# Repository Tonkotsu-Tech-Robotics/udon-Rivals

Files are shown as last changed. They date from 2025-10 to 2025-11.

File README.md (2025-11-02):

# UDON V2 | Rivals Robotics Competition
UDON V2 ISO Picture:
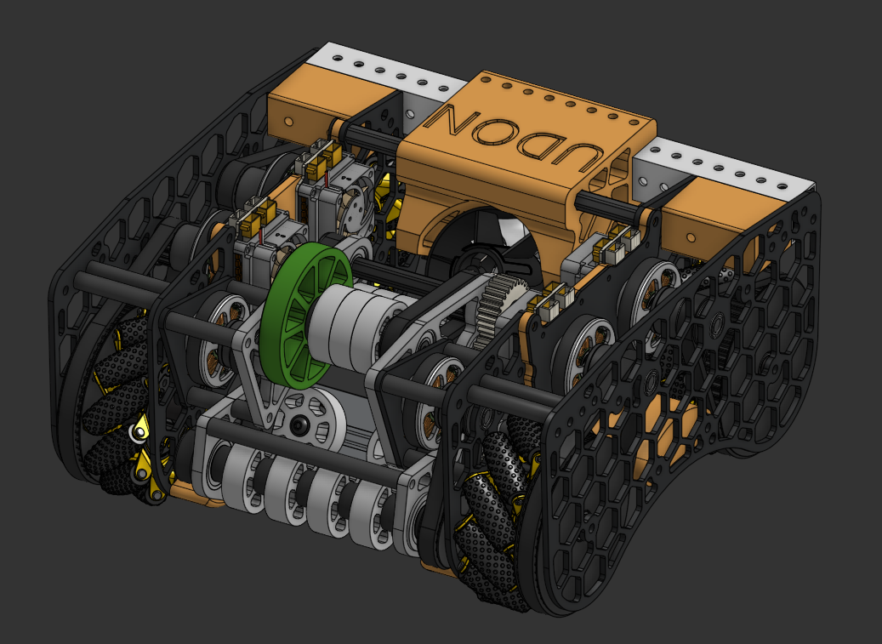
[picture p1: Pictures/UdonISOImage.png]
UDON ISO render


Onshape Link:
https://cad.onshape.com/documents/64d3a7b3a5a997c633685ba5/w/7495e428fcc4a5cb4c65dc9c/e/3e5da57740d178980547a374 

Feel free to make a copy and use it as a base for your robot!

## Rival Robotics
RIVAL Robotics Competition is a robotics competition for all ages targeted at advanced builders. There are multiple events with a different challange each year. For more information, visit https://www.rivalrobotics.co/

## Highlights
- 12x12 Mecanum Drive Base
- Compliant Shuttlecock Intake
- L1, L2 Shooter
- EDF Blower
- Silo Dumper

## Overview
UDON V2 is a shooter robot meant to compete in the Rival Robotics Competition. Its main goal is to shoot missiles (badminton shuttlecock) onto platforms on the goal post.

<table>
  <tr>
    <td valign="top" width="80%">
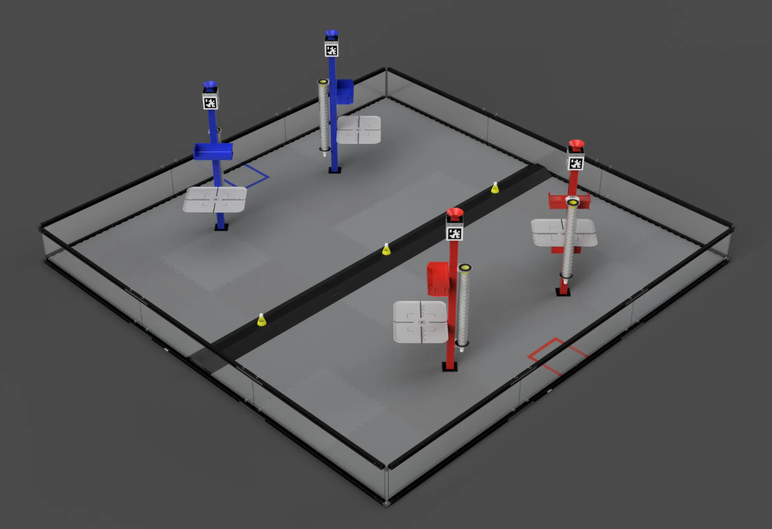
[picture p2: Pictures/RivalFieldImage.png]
Field ISO Render
      
    </td>
    <td valign="top">
        Image of the Rival Robotics "DOOMSDAY" Field
    </td>
  </tr>
</table>

This robot intakes the missiles off the ground to shoot it up into the L2 platforms. It also has the ability to "silo dump" or drop all the missiles out of the tube. The EDF on the back of the robot allows for large area "acquisition" of the missiles and blow it to the other side.

### Why?
UDON V2 was created in order to explore further levels of advanced robotics. Coming from an FRC and Robotics background, UDON acts as a way to build and learn skills as well as grow the RIVAL community. Tonkotsu Tech, the overarching group overseeing UDON, has made contributions to RIVALS and wishes to continue that through UDON.

## Pictures:
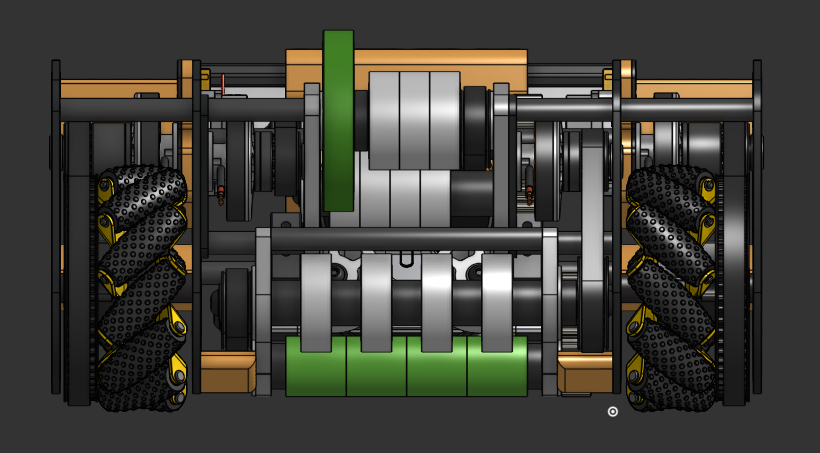
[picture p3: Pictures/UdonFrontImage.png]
UDON Front View

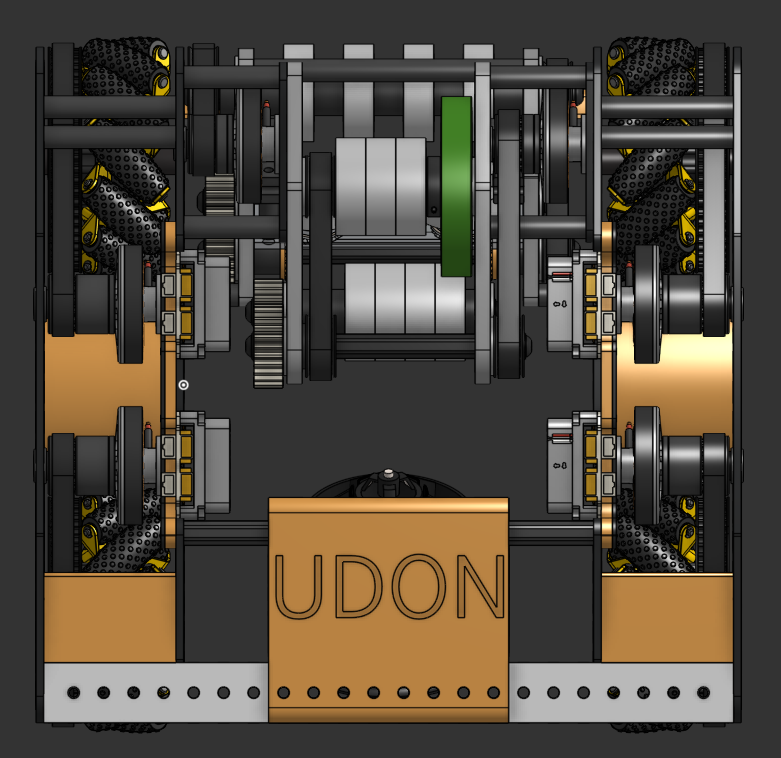
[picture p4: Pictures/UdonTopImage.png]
UDON Top View


## Control System
UDON V2 is based off the moteus control system (https://mjbots.com/) which is a high precision control system with the Raspberry Pi 4 at its core. 

- Raspberry Pi 4
- pi3Hat r4.5
- moteus-r4 Motor Controller
    - Controls 6 5010 Brushles Motors
- mjpower-ss

## Bill of Materials List:

You can download the full CSV here: [bom.csv](bom.csv)
<table>
  <colgroup>
    <col width="8%" />
    <col width="62%" />
    <col width="10%" />
    <col width="8%" />
    <col width="6%" />
    <col width="6%" />
  </colgroup>
  <thead>
    <tr>
      <th align="left">Vendor</th>
      <th align="left">Item</th>
      <th align="right">SKU</th>
      <th align="right">Cost</th>
      <th align="right">Amount</th>
      <th align="right">Total</th>
    </tr>
  </thead>
  <tbody>
    <tr>
      <td>WCP</td>
      <td>1.625" OD x 1/2" Wide Straight Flex Wheel (1/2" Hex Stretch, 30A)</td>
      <td align="right">WCP-1281</td>
      <td align="right">$2.99</td>
      <td align="right">4</td>
      <td align="right">$11.96</td>
    </tr>
    <tr>
      <td>WCP</td>
      <td>1.625" OD x 1/2" Wide Straight Flex Wheel (1/2" Hex Stretch, 45A)</td>
      <td align="right">WCP-1282</td>
      <td align="right">$2.99</td>
      <td align="right">9</td>
      <td align="right">$26.91</td>
    </tr>
    <tr>
      <td>WCP</td>
      <td>.375" OD x .159" ID Rounded Hex Stock (36")</td>
      <td align="right">WCP-0911</td>
      <td align="right">$19.99</td>
      <td align="right">1</td>
      <td align="right">$19.99</td>
    </tr>
    <tr>
      <td>WCP</td>
      <td>43t x 9mm Wide Timing Belt (HTD 5mm)</td>
      <td align="right">WCP-0511</td>
      <td align="right">$3.99</td>
      <td align="right">2</td>
      <td align="right">$7.98</td>
    </tr>
    <tr>
      <td>WCP</td>
      <td>Shipping + Tax</td>
      <td align="right"></td>
      <td align="right">$25.41</td>
      <td align="right">1</td>
      <td align="right">$25.41</td>
    </tr>
    <tr>
      <td>SWYFT</td>
      <td>HTD 5mm Pitch Timing Belts 75T 9mm</td>
      <td align="right"></td>
      <td align="right">$2.74</td>
      <td align="right">4</td>
      <td align="right">$10.96</td>
    </tr>
    <tr>
      <td>SWYFT</td>
      <td>HTD 5mm Pitch Timing Belts 50T 9mm</td>
      <td align="right"></td>
      <td align="right">$2.49</td>
      <td align="right">1</td>
      <td align="right">$2.49</td>
    </tr>
    <tr>
      <td>SWYFT</td>
      <td>HTD 5mm Pitch Timing Belts 45T 9mm</td>
      <td align="right"></td>
      <td align="right">$2.49</td>
      <td align="right">1</td>
      <td align="right">$2.49</td>
    </tr>
    <tr>
      <td>SWYFT</td>
      <td>Shipping Costs</td>
      <td align="right"></td>
      <td align="right">$10.55</td>
      <td align="right">1</td>
      <td align="right">$10.55</td>
    </tr>
    <tr>
      <td>Fabworks</td>
      <td>Mecanum Frame Plates</td>
      <td align="right">25-10-5300</td>
      <td align="right">$142.10</td>
      <td align="right">1</td>
      <td align="right">$142.10</td>
    </tr>
    <tr>
      <td>Amazon</td>
      <td>4010 Fans 12V - 8500RPM</td>
      <td align="right"></td>
      <td align="right">$8.99</td>
      <td align="right">1</td>
      <td align="right">$8.99</td>
    </tr>
    <tr>
      <td>Amazon</td>
      <td>CNHL 2200mAh 4S Lipo Battery 40C</td>
      <td align="right"></td>
      <td align="right">$39.99</td>
      <td align="right">1</td>
      <td align="right">$39.99</td>
    </tr>
    <tr>
      <td>Amazon</td>
      <td>Tax</td>
      <td align="right"></td>
      <td align="right">$3.80</td>
      <td align="right">1</td>
      <td align="right">$3.80</td>
    </tr>
    <tr>
      <td></td>
      <td></td>
      <td></td>
      <td></td>
      <td align="right">28</td>
      <td align="right">$313.62</td>
    </tr>
  </tbody>
</table>
BOM Google Sheet: https://docs.google.com/spreadsheets/d/1sjlqb2LRXWe4DsiQw7wpXGaVzfJAuZjR17yt-ZodIWk/edit?usp=sharing

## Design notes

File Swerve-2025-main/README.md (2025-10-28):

# Swerve-2025

A Python implementation of a swerve drive control system for robotics applications.

## Overview

This project provides a modular swerve drive system that controls four swerve modules, each consisting of a drive motor and a steering motor. The system uses the moteus motor controller library with Pi3Hat for communication.

## Features

- Asynchronous motor control using asyncio
- Modular swerve drive architecture
- Support for moteus motor controllers
- Individual module control with speed and angle settings
- Built-in test functions for system validation

## Requirements

- Python 3.7+
- Hardware: moteus motor controllers with Pi3Hat

## Installation

1. Clone the repository:
```bash
git clone https://github.com/Tonkotsu-Tech-Robotics/Swerve-2025.git
cd Swerve-2025
```

2. Install the required dependencies:
```bash
pip install -r requirements.txt
```

## Usage

### Basic Usage

Run the main program:
```bash
python main.py
```

### Hardware Configuration

The system is configured for the following motor layout:
- Bus 1: Drive motor ID 11, Steer motor ID 12
- Bus 2: Drive motor ID 13, Steer motor ID 14
- Bus 3: Drive motor ID 15, Steer motor ID 16
- Bus 4: Drive motor ID 17, Steer motor ID 18

## Dependencies

- asyncio: Asynchronous programming support
- moteus: Motor controller library
- moteus-pi3hat: Pi3Hat communication interface
- wpilib: WPILib robotics library
- wpimath: WPILib math utilities
- pygame: Game development library (for potential joystick input)

## License

This project is licensed under the terms specified in the LICENSE file.

## Contributing

1. Fork the repository
2. Create a feature branch
3. Make your changes
4. Submit a pull request

## Safety Notes

- Ensure proper hardware connections before running the program
- Use appropriate safety measures when working with motors
- Test in a controlled environment before deployment

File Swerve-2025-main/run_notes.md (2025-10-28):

# Setup Guide

Follow the moteus install docs available at

https://github.com/mjbots/pi3hat/blob/master/docs/reference.md#usage-with-client-side-tools

(I'll put the commands down here to run if you are too lazy like I was)

```
sudo apt install python3-pyside2* python3-serial python3-can python3-matplotlib python3-qtconsole libraspberrypi-dev

python -m venv --system-site-packages moteus-venv

sudo bash

source moteus-venv/bin/activate

pip install asyncqt importlib_metadata pyelftools

pip install moteus moteus_gui moteus-pi3hat
```

In the rasp pi, run these commands to get started with running any of the python files

```
sudo bash # Important since you'll have to run the python files in root
cd Swerve-2025
source moteus-venv/bin/activate # If moteus-venv does not exist, follow moteus guide on creating venv and installing required libraries
```

# Motor setup

You will have to figure out what motors you have first (as well as their ids) before doing any calibration. You can run this command to do that.

```
python3 -m moteus.moteus_tool --info
```

NOTE: If you have more than one motor you want to tune, you will have to adjust their IDs individually.

After figuring out what motors you have, run this command:

```
python3 -m moteus_gui.tview -t [motor id]
```

NOTE: If you want to have multiple motors, it can be dash-separated for a range or comma-separated for individual motors. Examples are given below.

Ex: Comma-separated values for tview in ids 11 and 12
```
python3 -m moteus_gui.tview -t 11,12
```

Ex: Dash-separated for tview in ids 1 through 15
```
python3 -m moteus_gui.tview -t 1-15
```

Dash-separated values can be useful for calibration, motor id lookup and looking at the values for multiple motors.

Comma-separated values can be useful for looking at the stats of a single motor at a time.

You may want to change the IDs so they aren't overriding each other (which can happen if there is improper configuration).

You will want to reopen tview if you have it open already (otherwise open it if you don't), but run this command instead:

```
python3 -m moteus_gui.tview -t [current motor id], [desired motor id]
```

Afterwards, go to the terminal in the bottom of tview and run the following:
```
[current id]>conf set id.id [desired id]
```
Wait for the desired ID to be set and for the terminal to reconfigure some stuff, before running this command:
```
[desired id]>conf write
```
You will know if you did it right if after running `[desired id]>conf write`, you get a console message that says `OK`. 

As an example usage of this, I have a motor on ID 3 and want to change that motor to ID 15. I will need to run the following:
```
python3 -m moteus.tview -t 3,15
```
Wait for motors to get configured up.
```
3>conf set id.id 15
```
Wait for tview to redo some configurations
```
15>conf write
```

Quick rundown of the commands we just ran:

The first command opens up tview for IDs 3 and 15. This is needed since the configuration changes right away and as soon as you change the ID to a new one, the motor will no longer be accessible on the old ID.

The second command simply calls on ID 3 to change its motor ID to 15.

The third command calls on the newly set ID 15 to write its changes so that its persistant.

# Calibration

To properly calibrate motors for code running, run this command in the shell AFTER you have sourced into the virtual environment

IMPORTANT: While calibrating, make sure any motor that is being calibrated can freely spin!

If you want to calibrate multiple motors (on different can busses), [motor id here] should be comma-separated

```
python3 -m moteus.moteus_tool -t [motor id here] --calibrate
```

Ex for 2 motors:
```
python3 -m moteus.moteus_tool -t 1,2 --calibrate
```

# Starting the motors

There are several example files that should work fine after calibration, the one that should be used is wait_complete.py.

https://github.com/mjbots/moteus/blob/main/lib/python/examples/wait_complete.py

Before starting motors, make sure to disable servopos position min/max (You only have to do this the first time setting up from the Raspberry Pi). You can do this by first going into tview

```
python3 -m moteus_gui.tview -t [all your motor ids, comma separated]
```

Then, in the command bar at the bottom of the GUI, running

```
[motor id]>conf set servopos.position_min nan
```
```
[motor id]>conf set servopos.position_max nan
```

then running this command to save the configurations

```
[motor id]>conf write
```

IMPORTANT: If you have multiple motors, you will have to run this command for each individual motor in order to prevent issues. If you did it incorrectly, running any code should show error 39 in the fault section of servo_stats in tview. You can check if you did it correctly in tview by running this command in the bottom terminal of tview:

```
[motor id to check]>d stop
[motor id to check]>d pos 20 0 0.5 a5 v5
[motor id to check]>d stop
```

Example usage:
```
12>d stop
12>d pos 20 0 0.5 a5 v5
12>d stop
```

(This will set the position to 20 with an ending velocity of 0, torque of 0.5, and max accel of 5 rev/s^2 and max velocity of 5 rev/s, then stop the motor).

NOTE: In order to completely check for faults, you may want to run that more than once (2 times should be fine).

Setting servo pos max/min to NaN will disable the check that requires the motor position to start within a specific range (from -1 to 1), and this can screw up the motors if you don't have a command that moves the motors into their original starting position.

# Additional Notes

Running the tview GUI will also allow you to graph and track motor telemetry data such as current position, velocity, among other points, making it easier to debug

Viewing errors or faults can be done by going into tview, then servo_stats, and then fault.

SUPER IMPORTANT!!!!!! In any motor.set_position() or motor.set_position_wait_command() function, ALWAYS have a velocity_limit and accel_limit parameter or else ur motor go bye bye :D An example of such is provided down below.

```
await controller.set_position( # Same thing with controller.set_position_wait_complete()
    position=1.0,
    velocity=2.0,
    velocity_limit=5.0,
    accel_limit=4.0
)
```

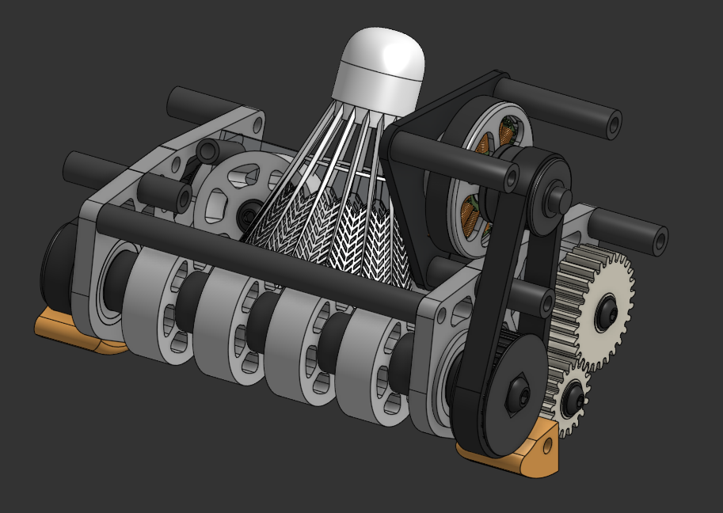
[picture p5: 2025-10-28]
Pictures/IntakeOnlyImage.png

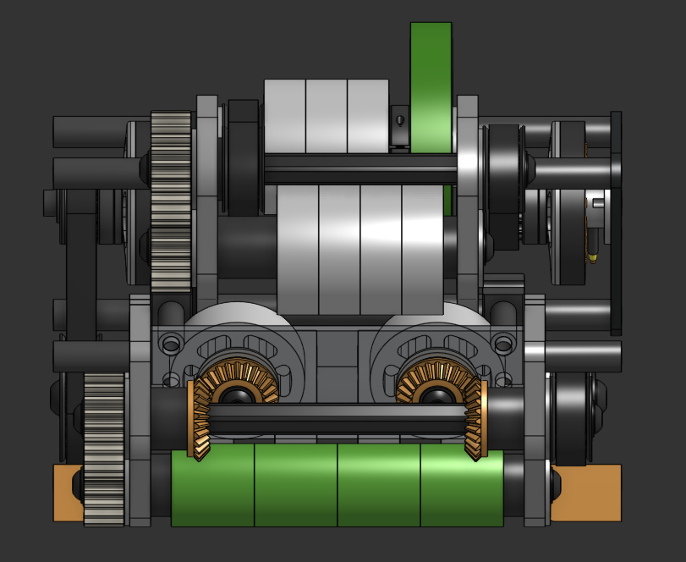
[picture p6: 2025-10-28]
Pictures/IntakeBackImage.png

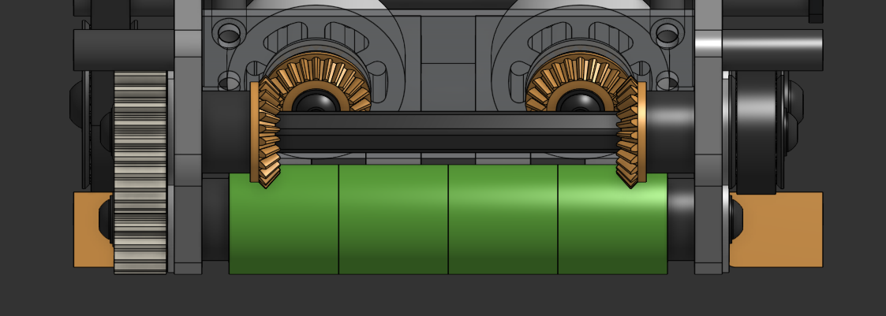
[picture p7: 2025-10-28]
Pictures/BevelGearShowing.png

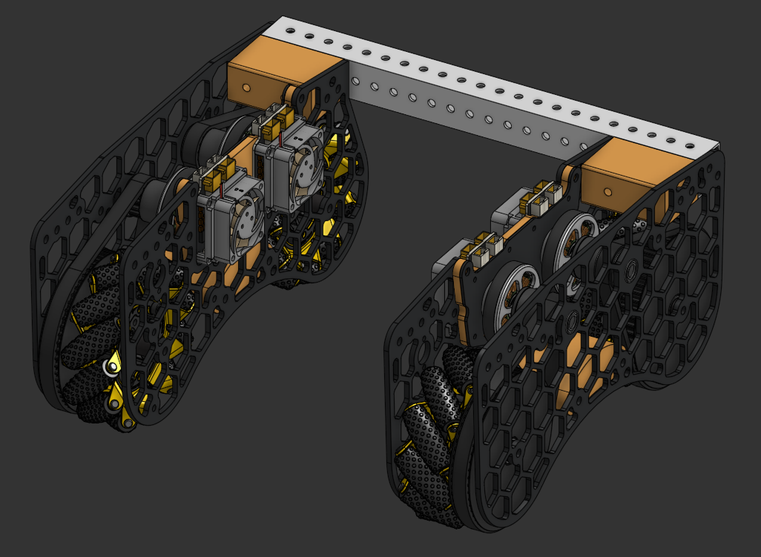
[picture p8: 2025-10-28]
Pictures/BareMecanumDrive.png

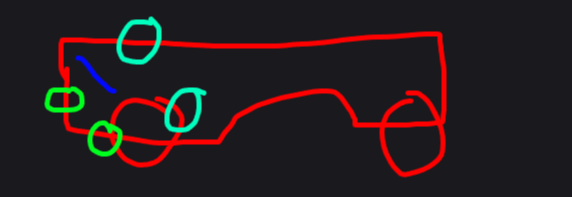
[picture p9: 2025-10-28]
Pictures/UDONSketch.png

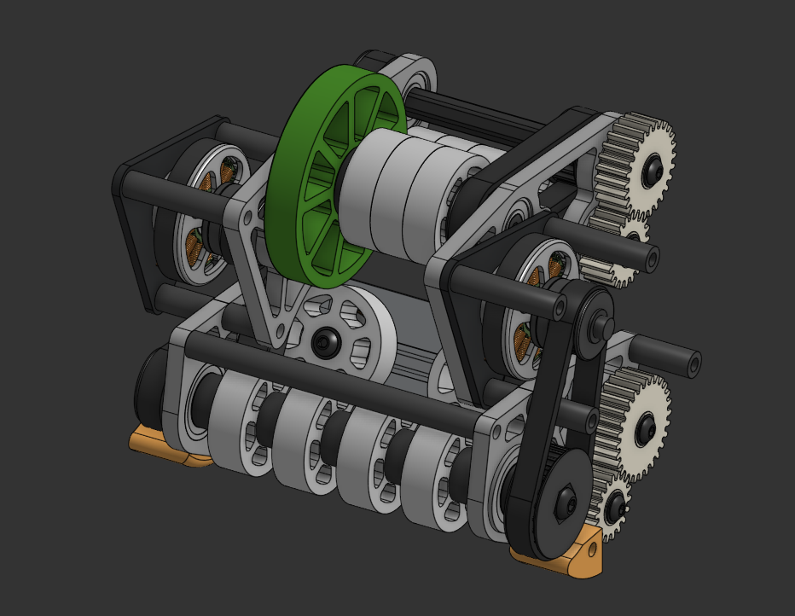
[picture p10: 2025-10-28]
Pictures/IntakeISOImage.png

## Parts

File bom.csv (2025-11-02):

Vendor | Item | SKU | Cost | Amount | Total
WCP | 1.625" OD x 1/2" Wide Straight Flex Wheel (1/2" Hex Stretch, 30A) | WCP-1281 | $2.99 | 4 | $11.96
WCP | 1.625" OD x 1/2" Wide Straight Flex Wheel (1/2" Hex Stretch, 45A) | WCP-1282 | $2.99 | 9 | $26.91
WCP | .375" OD x .159" ID Rounded Hex Stock (36") | WCP-0911 | $19.99 | 1 | $19.99
WCP | 43t x 9mm Wide Timing Belt (HTD 5mm) | WCP-0511 | $3.99 | 2 | $7.98
WCP | Shipping + Tax |  | $25.41 | 1 | $25.41
SWYFT | HTD 5mm Pitch Timing Belts 75T 9mm |  | $2.74 | 4 | $10.96
SWYFT | HTD 5mm Pitch Timing Belts 50T 9mm |  | $2.49 | 1 | $2.49
SWYFT | HTD 5mm Pitch Timing Belts 45T 9mm |  | $2.49 | 1 | $2.49
SWYFT | Shipping Costs |  | $10.55 | 1 | $10.55
Fabworks | Mecanum Frame Plates | 25-10-5300 | $142.10 | 1 | $142.10
Amazon | 4010 Fans 12V - 8500RPM |  | $8.99 | 1 | $8.99
Amazon | CNHL 2200mAh 4S Lipo Battery 40C |  | $39.99 | 1 | $39.99
Amazon | Tax |  | $3.80 | 1 | $3.80
 |  |  |  | 28 | $313.62

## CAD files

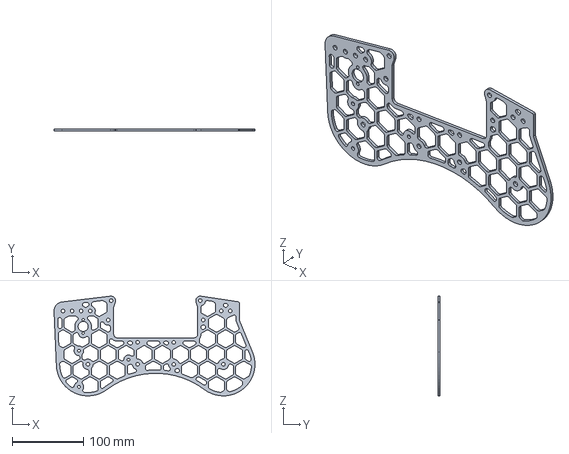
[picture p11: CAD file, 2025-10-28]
CAD/6061 Plates/Inside Plate.step
282.7 x 3.17 x 140.4 mm

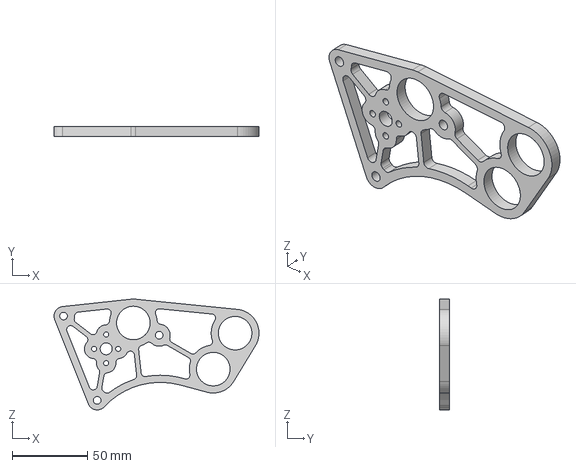
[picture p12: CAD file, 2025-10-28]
CAD/6061 Plates/Shooter Plate Right.step
136.1 x 6.35 x 73.6 mm

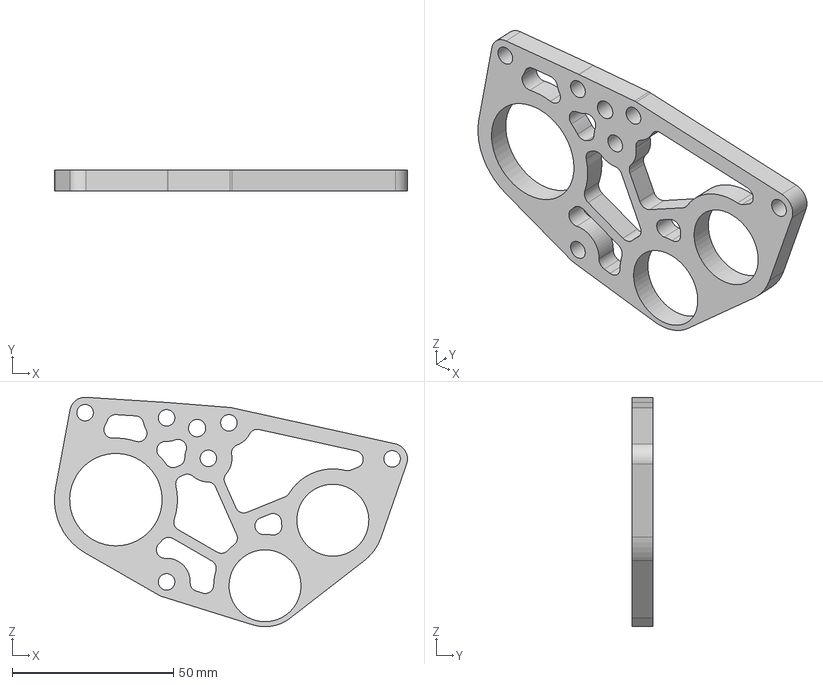
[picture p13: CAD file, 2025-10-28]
CAD/6061 Plates/Intake Plate.step
109.3 x 6.35 x 71.0 mm

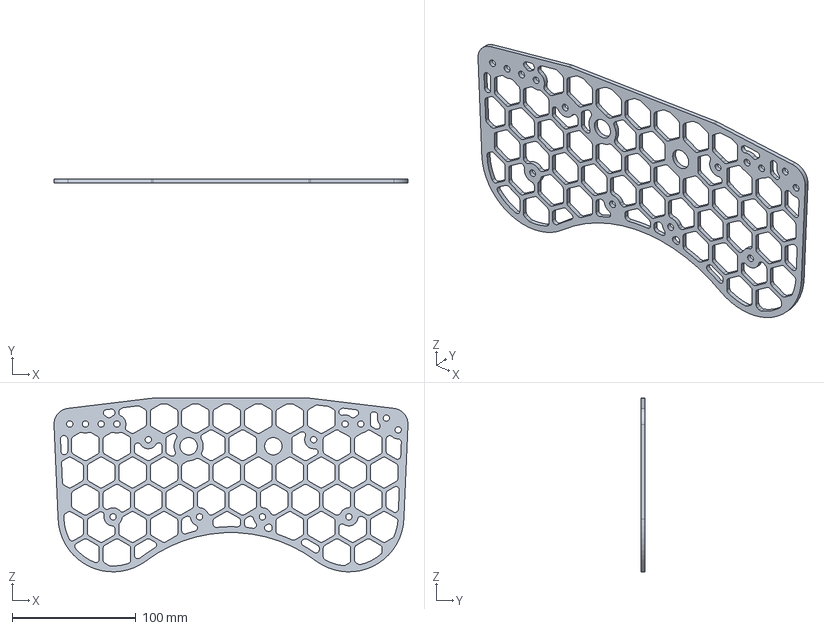
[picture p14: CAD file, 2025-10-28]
CAD/6061 Plates/Outside Plate.step
286.0 x 3.17 x 140.3 mm

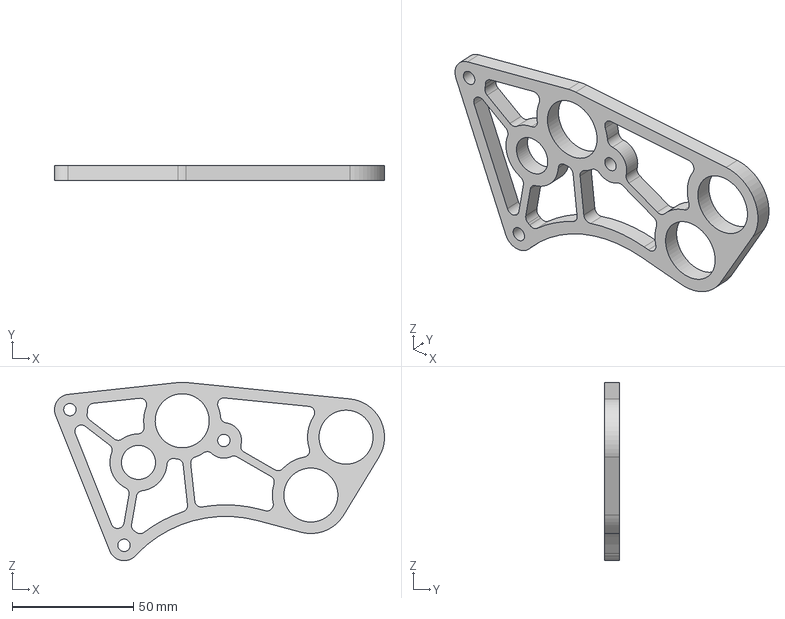
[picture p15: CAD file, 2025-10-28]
CAD/6061 Plates/Motor Plate Left.step
136.1 x 6.35 x 73.6 mm

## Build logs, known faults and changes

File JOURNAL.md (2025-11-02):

<!--
  ===================    !!READ THIS NOTICE!!   ====================
  DO NOT edit this file manually. Your changes WILL BE OVERWRITTEN!
  This journal is auto generated and updated by Hack Club Blueprint.
  To edit this file, please edit your journal entries on Blueprint.
  ==================================================================
-->

## 10/27/2025 7:42 PM - Restarting an Old project  

I've had multiple attempts at building a rival robot, many of which came into fruition but never had enough time to be tuned and refined. This includes Tonkotsu V1 and Tonkotsu V2 which had all the CAD and actual physical build but the swerve drive made it difficult to run well. With UDON, I plan to take a step back and build an easier mecanum drive. Here's what I'm thinking: 


Not great, I know but the mechanism can be changed. The red is the mecanum drive base, green is the intaking wheels, dark blue is the centering wheels, and teal is the shooter. I wanted to base this off NCR rivals bot but as a shooter design instead of an arm that they had. One of the biggest issues here is just how consistent it can be. With the swerve drive I already have, the moteus controllers have very good rpm control but I'm not really sure how well the shooter could consistently hit that same spot. 

Beginning to work on the mecanum drive here: 


Big decision I had to make was what the cool the moteus controllers with. The controllers in the CAD use fans because official heatsinks are ABSURDLY expensive, around 30 dollars each. I've had some controllers burn up in the past and don't wish for that to happen again. Another thing is for some reason, Onshape mirroring causes really bad lag... not really a design problem but something that is really annoying. Reusing what I had, I used the 5010 motor from the swerve but went with a different pinion mounting this time. Last time on the swerve, I bolted in a metal custom cut gear onto the motor directly and it caused a lot of friction between the gears so this time I'm belting it and also having a 3D print and connection to a pinion on top and then holding the other side with a bearing. I think this will help a lot with making the motor movement better (I think that friction caused the burn out of the moteus controller in the swerve).

I think this is a great start, I'm banking on the fact that I can also borrow the GoBilda mecanum wheels from my local FTC team :D  

## 10/27/2025 7:43 PM - CAD Intake  

I've thought about many ways to do the intake, with a shuttlecock being such an oriented-based game piece, the head has to go forward at all times for this to work. I tried to figure out a passive way of intaking but none seems as reliable as having 2 centering wheels.


I'm quite proud of the centering wheels using bevel gear tech, it just looks so good. One of the biggest issues here was trying to figure out how to power the centering wheels. I should have taken a photo of the interferences I was having before but at the time, I didn't plan on powering it using the same motor, I was thinking of just having a separate motor. However, the tight packaging between the mecanum drives didn't allow for another motor, especially because it was horizontal. There were many adjustments I had to make to the positioning of the shaft that holds the bevel gear.


Right now, I'm not exactly sure how I plan to stop the shuttlecock from going all the way through. I didn't find a good way to package and might be leaning towards a usb sensor that connects to the Raspberry Pi because all of the pins are covered by the moteus pi3hat. However, I want to first prototype whether I can get away without that and just not spin the shooter motors and back the shuttcock into place for shooting :)  

## 10/27/2025 7:44 PM - Finished Shooter CAD  

Finally, I found a way to fit in this shooter. The packaging is quite tough and I am slightly worried over the flywheels expanding when it is shooting. I think this is good enough. One other thing is that the green wheel is used for silo dumping but it might get in the way of the shuttlecock, I have to prototype to find out.



I had to commit to the angle as I wasn't going to go back on it. Looking at the arc, it looks okay for shooting but what isn't prototyped yet is the compression. I estimated a 5mm compression out of a 25mm shuttlecock head would be decent but I will never know without trying it. For future journals, I need to start taking more pictures when things go wrong. As said before, packaging was a huge issue, I couldn't figure out how to make the shafts and pullies not touch the side plates. I ended up opting just to have another shaft that goes across so I can split each side evenly with the gears and pullies. 



But now I'm looking back on it, this packaging also means repairability is kind of on the iffy side. Getting to a bolt in this intake is a little bit sus... looking to fix that.  

## 10/27/2025 7:45 PM - EDF Blower Add-on  

Watching back some of the old games from Orange County Maker Fair and Tidal Tumble, EDF seems like the way to go. The EDF blows the shuttlecocks to the other side and since the floor is a point, that is a LOT of points that can be gained that way. I added one to the robot too but I think it needs a cover because in one of the matches, I saw a shuttlecock go into it and it just exploded.



It looks really good but now I have to go back and redesign where I am going to put my electronics. I planned to put it where the EDF is (in the back of the robot) but with that space gone, I might have to add a plate so that I can just put the electronics on the top of the bot. This isn't really ideal because I liked the idea of a flat tanky robot but oh wells.


Credits: NCR 

This is one of the things I need to do in the future. I loved how they packaged their raspberry pi and moteus pi3hat but I'm not sure if I want to do the way they did. On my Raspberry pi stack right now, I have a fan in between to cool the pi but that also means it will be a lot taller. Considering whether I should follow NCR or not...  

## 10/28/2025 - Blueprint!  

Hey everyone! 

I didn't do much today besides just figuring out this blueprint stuff. I got the BOM stuff done and now the project is shipped off! 


Thanks so much for the follows and the views, I hope to be able to show you my progress soon. I'm starting prototyping with 3D prints, especially the intake. One issue I might be seeing is just manufacturing fast enough. Rivals competition is on November 22 so time is of the essence. Thanks for checking this out!

## 10/30/2025 - Fixed My Journals  

Hey everyone!

Update: After shipping the project, I got feedback that I need to fix my journals and make them more in depth with my struggles and my successes. I went back and added a lot of the key parts that I remember. Sorry if I couldn't have much images of all the troubles I had (so many interferences in Onshape because packaging was really tight) but I hope my words are good enough for now. 100% for the future, I will document more and not just take pictures when the final product is done. 


I went ahead and printed some of parts in the intake and shooter. I know it says in the github to cut this out of 6061 aluminum but actually, I found that 3D printing should be strong enough for prototyping. There is some bends so I will go back and print this with no pocketing. Right now, its at an absurd 8 walls and 35% infill and seems to be holding up good!

I hope you all enjoy! See you in the next journal :D

P.S. Got an update from my very first journal, my FTC team was willing to lend me their mecanum wheels! That saves me over 180 dollars :) One bad thing though, went to my FRC team to see if I could use the CNC router to cut the aluminum and it seems like the router isn't working right now... hoping to see if I can help fix it for them and save some more money.  

## 11/2/2025 - Getting This Approved  

Hey everyone!

Sorry for the lack of posts in recent days, I've been talking and working with some Hack Club/Blueprint people that helped me get this approved/into what they want from the project. I truly appreciate all the help from Hack Club members, they are amazing. One of the biggest things that I need to change is just making my BOM cheaper. The way I did this was removing the EDF as it was the one thing in the project that wasn't a stepping stone to build the rest. This was quite sad as I really liked the EDF but unlike the mecanum plates, I need those plates to build the rest of the robot. The EDF can always be added on at the end. 


Here's what it'll look like without the EDF. This was a hard decision but I had to do something to drop the price and be reasonable. I am now down around 80 dollar from the original sitting around $313 instead of $397. I'm not sure whether or not these changes count for hours yet so I will be in contact with Hack Club, for now, I'll just put 0.1 hours.

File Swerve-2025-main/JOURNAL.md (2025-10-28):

<!--
  ===================    !!READ THIS NOTICE!!   ====================
  DO NOT edit this file manually. Your changes WILL BE OVERWRITTEN!
  This journal is auto generated and updated by Hack Club Blueprint.
  To edit this file, please edit your journal entries on Blueprint.
  ==================================================================
-->

## 10/27/2025 - Test  

I'm trying to test whether i need to make a journal in here or the journal in github because the one In github, apparently the hours don't transfer onto the actualhours on the website

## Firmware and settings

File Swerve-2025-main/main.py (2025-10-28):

import asyncio
from Swerve.SwerveDrive import SwerveDrive

async def main(swerve_drive: SwerveDrive = None):
    await swerve_drive.initialize_modules()
    speeds = [0.0, 0.0, 0.0]
    while True:
        speeds = await swerve_drive.getControllerSpeeds()
        await swerve_drive.set_drive_speeds(speeds[0], speeds[1], speeds[2], False)

        
    
if __name__ == '__main__':
    # Initialize SwerveDrive instance
    swerve_drive = SwerveDrive()
    try:
        asyncio.run(main(swerve_drive))
    except KeyboardInterrupt:
        print("Program interrupted by user. Stopping all modules.")
        asyncio.run(swerve_drive.stop())
        exit(0)
    except Exception as e:
        print(f"An unexpected error occurred: {e}")
        asyncio.run(swerve_drive.stop()) 

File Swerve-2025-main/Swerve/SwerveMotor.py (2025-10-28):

import moteus
import moteus_pi3hat
import asyncio
import math

"""
A swerve motor class

Defines all the functions required for motor movement using the moteus library.
"""
class SwerveMotor:
    def __init__(self,
                 motorID: int,
                 transport: moteus_pi3hat.Pi3HatRouter,
                 accel_limit: float=20.0,
                 velocity_limit: float=20.0,
                 watchdog_timeout: float=0.5):
        """
        Constructs a swerve motor instance.

        :param motorID (int): Moteus controller ID.
        :param transport (Pi3HatRouter): Transport object.
        :param accel_limit (float): Acceleration limit in rev/s².
        :param velocity_limit (float): Velocity limit in rev/s.
        :param watchdog_timeout (float): Timeout before function stops running (if you don't know how this param works, better not touch it).
        """

        # Set the local properties to be accessible from within the class.
        self.accel_limit = accel_limit
        self.velocity_limit = velocity_limit
        self.watchdog_timeout = watchdog_timeout
        self.motor = moteus.Controller(id=motorID, transport=transport)

    @property
    async def position(self):
        """
        Gives the current absolute motor position (relative to position 0).

        :return float: The current absolute motor position in revolutions.
        """

        # Query the motor for its current state
        result = await self.motor.set_position(position=math.nan, query=True)

        print(f"Motor {self.motor.id} position register is of type {type(result.values[moteus.Register.POSITION])}")

        # Extract the position from the result
        return result.values[moteus.Register.POSITION]

    @property
    async def velocity(self) -> float:
        """
        Gives the current velocity

        :return float: The current velocity of the motor in rev/s.
        """

        # Query the motor for its current state
        result = await self.motor.set_position(position=math.nan, query=True)

        # Extract the position from the result
        return result.values[moteus.Register.VELOCITY]
    
    @property
    async def values(self) -> list:
        """
        Gives a list of properties exposed by the moteus library for reading or writing.
        The full list can be found here:
        https://github.com/mjbots/moteus/blob/main/lib/python/moteus/moteus.py#L149 (class code)
        https://github.com/mjbots/moteus/blob/main/docs/reference.md#a2b-registers (descriptors)
        
        :returns [any]: A list of Register object properties
        """
        result = await self.motor.set_position(query=True)

        return result.values

    async def setAngle(self, angle_deg: float, transport: moteus.Transport) -> bool:
        """
        A position mode function.
        
        Move to a target angle in degrees.
        Returns boolean and retrived position after rotation

        NOTE: If the wait_time parameter is not set, set_position will not fully run unless you manually implement asyncio.sleep().
        It is better if you implement this yourself IF you have more than 1 motor.

        :param angle_deg (float): An angle in degrees to move to. Will be converted to revolutions. Motor will move  to this angle relative to its current position, and with a max speed of what is set in self.velocity_limit in rev/s. It will reach this max speed in self.accel_limit in rev/s².
        :param transport (moteus.Transport): The transport object to use for communication. Should be the same transport used in every motor.

        :return bool: True if the angle was set successfully, False otherwise.
        """

        try:
            angle_rev = angle_deg / 360.0

            # degAngle = await self.position * 360

            # if degAngle == None:
            #     raise TypeError(
            #         "Degree angle in setAngle function returned as type None")

            # adjustedAngle = angle_rev  # temp angle for now, add calculations in later

            await transport.cycle([self.motor.make_position(
                position=angle_rev,
                accel_limit=self.accel_limit,
                velocity_limit=self.velocity_limit,
                watchdog_timeout=self.watchdog_timeout
            )])

            return True
        except Exception as e:
            print(f"Error caught in setAngle function: {e}")
            await self.emergency_stop(f"Error caught in setAngle function: {e}")
            return False

    async def addToCurrentPos(self, position_val: float, transport: moteus.Transport) -> bool:
        """
        Move to a position in revolutions relative to current position.

        NOTE: If the wait_time parameter is not set, set_position will not fully run unless you manually implement asyncio.sleep().
        It is better if you implement this yourself IF you have more than 1 motor.

        :param position_val (float): The position target to move to in revolutions. This will be added to the current position of the motor, not set as an absolute position.
        :param transport (moteus.Transport): The transport object to use for communication. Should be the same transport used in every motor.

        :return bool: True if the position was set successfully, False otherwise.
        """
        try:
            await transport.cycle([self.motor.make_position(
                position=(position_val + self.position),
                accel_limit=self.accel_limit,
                velocity_limit=self.velocity_limit,
                watchdog_timeout=self.watchdog_timeout)
            ])

            return True
        except Exception as e:
            print(f"Error caught in addToCurrentPosition function: {e}")
            await self.emergency_stop(f"Error caught in addToCurrentPosition function: {e}")
            return False

    async def setPosition(self, position_val: float, transport: moteus.Transport ) -> bool:
        """
        A position mode function.

        Move to an absolute position in revolutions.

        NOTE: If the wait_time parameter is not set, set_position will not fully run unless you manually implement asyncio.sleep().
        It is better if you implement this yourself IF you have more than 1 motor that you want to run.

        :param position_val (float): The position target to move to in revolutions.
        :param transport (moteus.Transport): The transport object to use for communication.

        :return bool: True if the position was set successfully, False otherwise.
        """
        try:
            await transport.cycle([self.motor.make_position(
                position=position_val,
                accel_limit=self.accel_limit,
                velocity_limit=self.velocity_limit,
                watchdog_timeout=self.watchdog_timeout)
            ])
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

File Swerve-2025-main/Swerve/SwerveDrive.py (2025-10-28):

import moteus
import moteus_pi3hat
import asyncio
from Swerve.SwerveModule import SwerveModule
import Utils.Constants as Constants
import wpimath.estimator as estimator
from wpimath.geometry import Pose2d, Rotation2d
import wpimath.kinematics 
from wpimath.geometry import Pose3d, Rotation3d
import math
import wpilib
import numpy as np


from Utils.Controller import Controller

class SwerveDrive:
    def __init__(self):
        self.transport: moteus.Transport = moteus_pi3hat.Pi3HatRouter(
            servo_bus_map={
                1: [11, 12], # Bus 1, Motor ids 11 and 12
                2: [13, 14], # Bus 2, Motor ids 13 and 14
                3: [15, 16], # Bus 3, Motor ids 15 and 16
                4: [17, 18],  # Bus 4, Motor ids 17 and 18
            }
        )

        #need to add controller
        self.controller = Controller()
        self.modules = []
        # pose_estimator: estimator.SwerveDrive4PoseEstimatorBase | None = None
        # pose_estimator_3d: estimator.SwerveDrive4PoseEstimator3dBase | None = None

        # states = [wpimath.kinematics.SwerveModuleState() for _ in range(4)]
        # set_states = [wpimath.kinematics.SwerveModuleState() for _ in range(4)]

        # self.pose_estimator = self.initialize_pose_estimator()
        # self.pose_estimator_3d = self.initialize_pose_estimator_3d()
        # self.field = wpilib.Field2d()

        # self.robot_pos = Pose2d(0.0, 0.0, Rotation2d.fromDegrees(0.0))
        # self.robot_pos_3d = Pose3d(0.0, 0.0, 0.0, Rotation3d(0.0, 0.0, 0.0))

    # this is not my code maybe delete later
    async def stop(self):
        """
        Stops all swerve modules.
        """
        [
            await module.stop() for module in self.modules
        ]

    async def setAll(self, speeds, angles):
        """
        Sets the speed and angle of each swerve module.
        """
        [
            await module.set(speed, angle, self.transport)
            for module, speed, angle in zip(self.modules, speeds, angles)
        ]

    async def setModule(self, index, speed, angle):
        """
        Sets the speed and angle of a specific swerve module.
        """
        await self.modules[index].set(speed, angle, self.transport)

    async def getModulePosition(self, index):
        """
        Gets the position of a specific swerve module.
        """
        return await self.modules[index].getPosition()
    
    async def getControllerSpeeds(self):
        """
        Uses the controller to set the speeds of the swerve modules based on joystick input.
        """
        forward_speed = self.controller.get_axis(Controller.LEFT_X)
        left_speed = self.controller.get_axis(Controller.LEFT_Y)
        turn_speed = self.controller.get_axis(Controller.RIGHT_X)

        return [forward_speed, left_speed, turn_speed]


    # NEW CODE

    async def initialize_modules(self):
        return [
            SwerveModule(
               drive_id=11, steer_id=12, transport=self.transport
            ),
            SwerveModule(
                drive_id=13, steer_id=14, transport=self.transport
            ),
            SwerveModule(
                drive_id=15, steer_id=16, transport=self.transport
            ),
            SwerveModule(
                drive_id=17, steer_id=18, transport=self.transport
            )
        ]
    
    # async def initialize_pose_estimator(self):
    #     return estimator.SwerveDrive4PoseEstimator(
    #         Constants.kinematics,
    #         Rotation2d.fromDegrees(self.get_heading()), #<- needs to be updated
    #         self.get_module_positions(), #<- allso wrong change later
    #         Pose2d(0.0, 0.0, Rotation2d.fromDegrees(0.0)),
    #         np.array([[0.02], [0.02], [math.radians(5)]]),
    #         np.array([[0.3], [0.3], [math.radians(10)]])
    #     )
    
    # async def initialize_pose_estimator_3d(self):
    #     return estimator.SwerveDrive4PoseEstimator3d(
    #         Constants.kinematics,
    #         self.get_rotation_3d_function, #<- needs to be updated
    #         self.get_module_positions(), #<- wrong change later
    #         Pose3d(0.0, 0.0, 0.0, Rotation3d(0.0, 0.0, 0.0))
    # )

    async def swerve_drive_periodic(self):
        # await self.update_pos() 
        return

        #idk why its white 
        # self.pose_estimator.update(self.get_pidgey_rotation(), self.get_module_positions()) #fix more stuff dummy
        # self.pose_estimator_3d.update(self.pidgey.getRotation3d(), self.get_module_positions()) # needs to change the rotation functions here

        # self.robot_pos = self.pose_estimator.getEstimatedPosition()
        # self.robot_pos_3d = self.pose_estimator_3d.getEstimatedPosition()

    # async def update_pos(self):
        # return #no idea how to do this shit rn
    
    async def set_drive_speeds(self, forward_speed, left_speed, turn_speed, is_field_oriented = False):
        # Convert to chassis speeds the robot understand?s
        speeds = None
        if is_field_oriented:
            speeds = wpimath.kinematics.ChassisSpeeds.fromFieldRelativeSpeeds
            (forward_speed, left_speed, turn_speed, self.get_heading_rotation2d())
            #fix get heading

        else: 
            speeds = wpimath.kinematics.ChassisSpeeds(forward_speed, left_speed, turn_speed)

        speeds = wpimath.kinematics.ChassisSpeeds.discretize(speeds, 0.02)

        new_states = Constants.kinematics.toSwerveModuleStates(speeds)

        new_states = wpimath.kinematics.SwerveDrive4Kinematics.desaturateWheelSpeeds(new_states, Constants.MAX_SPEED)
        await self.set_swerve_module_states(new_states)

    async def reset_heading(self):
        #reset the heading
        return

    async def get_swerve_module_states(self) -> wpimath.kinematics.SwerveModuleState:
        current_module_state = wpimath.kinematics.SwerveModuleState()
        for i in range(4):
            current_module_state[i] = self.states[i]
        
        return current_module_state
    
    async def set_swerve_module_states(self, states):
        set_states = states
        for i in range (4):
            self.modules[i].set_states(set_states[i])

    
    async def get_swerve_module_positions(self) -> wpimath.kinematics.SwerveModulePosition:
        current_module_position = wpimath.kinematics.SwerveModulePosition[4]
        for i in range(4):
            current_module_position[i] = await self.modules.get_position()
        
        return current_module_position
    
    async def stop_modules(self):
        for i in range(4):
            await self.modules[i].stop()
    
    async def reset_drive_positions(self):
        for i in range(4):
            await self.modules.reset_drive_positions()

    
    async def get_heading(self) -> float:
        result = await self.transport.cycle([], request_attitude=True)
        imu_result = [
            x for x in result
            if x.id == -1 and isinstance(x, moteus_pi3hat.CanAttitudeWrapper)][0]
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

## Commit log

2025-10-28 Added CAD step file
2025-10-28 Added CAD Files
    [Inside Plate.step, Intake Plate.step, Motor Plate Left.step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]
2025-10-28 BOM and Journal
    [UDON BOM - TEST Purchase.csv]
2025-10-28 Added Swerve for Sample Code
2025-10-28 BOM rename
    [bom.csv]
2025-10-28 fixed BOM
    [bom.csv]
2025-10-28 BOM fix
    [bom.csv]
2025-11-02 Bom Adjust
    [bom.csv]
